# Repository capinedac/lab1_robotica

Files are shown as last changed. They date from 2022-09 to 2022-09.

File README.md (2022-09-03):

# Laboratorio 1 - Robótica Industrial No.1 
Equipo de trabajo: 
- Luis Alberto Chavez Castro
- Camilo Pineda Correa
 
## Desarrollo de la herramienta
Para el proceso de fabricación de la herramienta, este se desarrolló primero físicamente, teniendo en cuenta las medidas de ajuste con el portaherramienta para su implementación, y a partir de este se generó el modelo CAD con ayuda del software Catia.
 
La herramienta tuvo una primera versión que fue probada, se puede visualizar en su montaje al robot articulado:
 
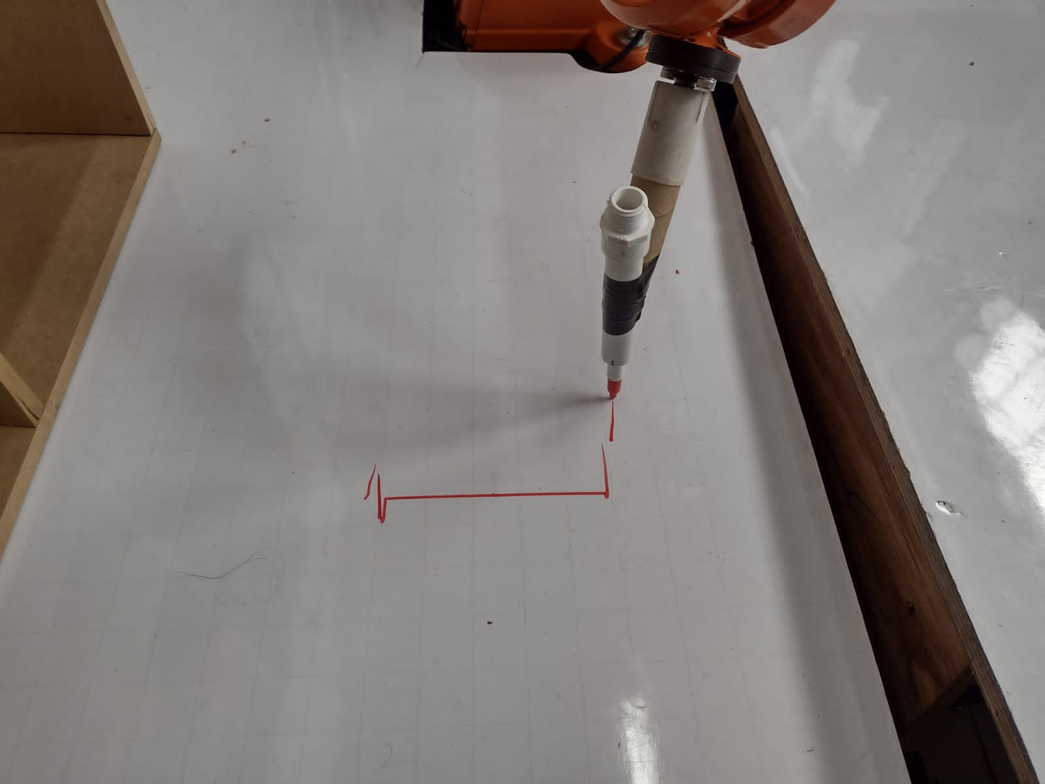
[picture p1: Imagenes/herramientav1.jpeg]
Herramienta v1

 
Su versión final diseñada es la siguiente:
 
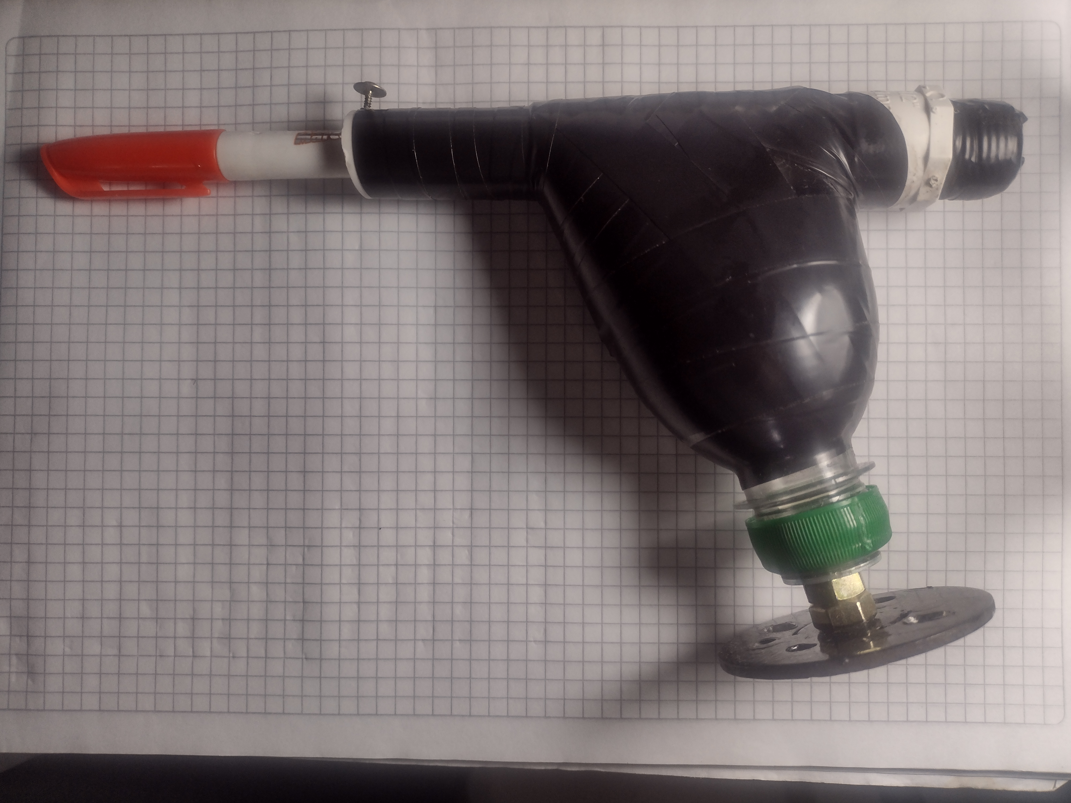
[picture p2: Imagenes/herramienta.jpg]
Foto herramienta

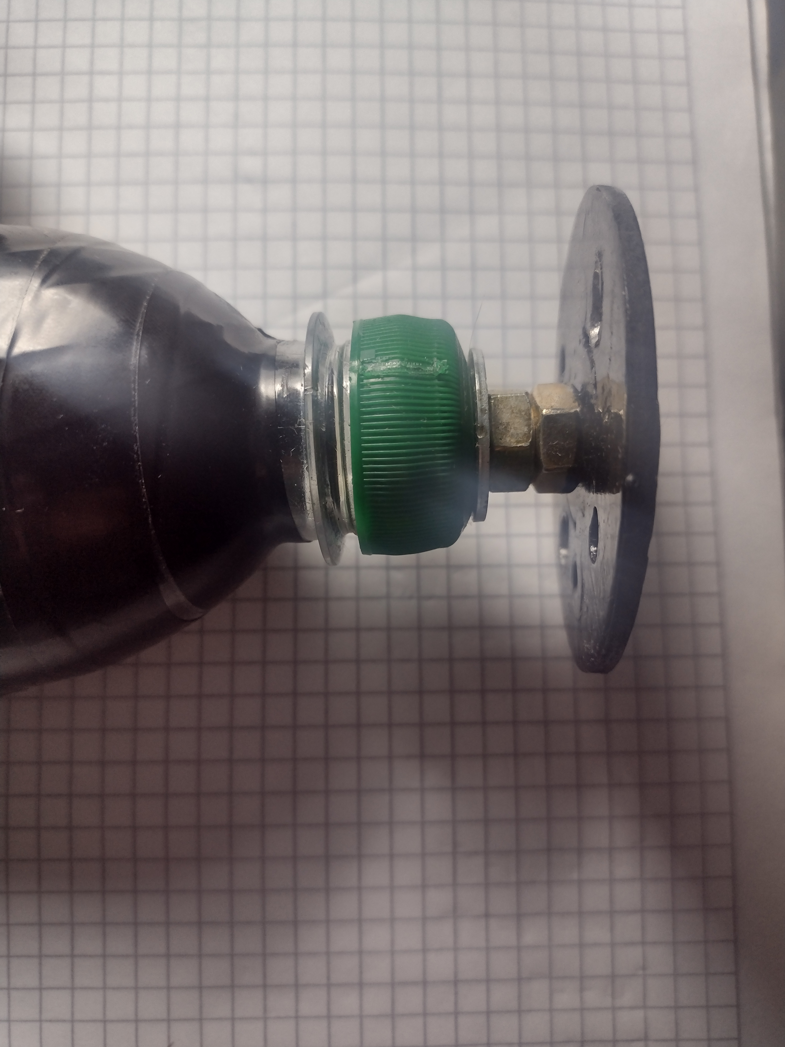
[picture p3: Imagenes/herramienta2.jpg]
Foto 2 herramienta

 
Y su modelo CAD obtenido fue:
 
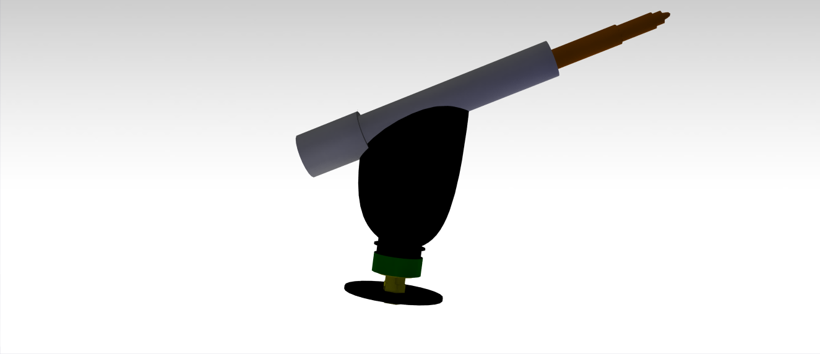
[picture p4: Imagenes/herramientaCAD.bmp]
CAD herramienta

 
Se construyó una herramienta inicial la cual se buscó desde un comienzo que su eje primitivo de diseño no se encontrara sobre el eje Z del TCP del plato portaherramientas a fin de evitar las singularidades del robot, para esto las dos primitivas de diseño empleadas fueron dos líneas coplanares que no fueran paralelas con un ángulo entre ellas de 120º.
Además al realizar las primeras pruebas con el manipulador, se encontró que la herramienta vibraba mucho y era inestable a la hora de ser colocada sobre la superficie plana para trazar, por lo que se planteó un incremento en los  momentos de inercia que evitase el movimiento de la pieza, sin embargo como uno de los requerimientos de diseño que presentados considera el bajo peso para la reducción de cargas inerciales del robot, se planteó emplear materiales pero todos en diferentes medidas incrementaron los momentos de inercia, así que se planteó realizar una ampliación de la geometría de la zona que presentaba la mayor oscilación con materiales ligeros, de fácil consecución y simétricos, para lo cual el candidato seleccionado resultó ser un envase PET (polietilen-Tereftalato) de agua de 500ml, el cual por su peso ligero y alta resistencia mecánica al desgaste por vibraciones, entregó un gran comportamiento al mantener el bajo peso y reducir considerablemente la vibración de la herramienta.

Además de la reducción de cargas inercial , el candidato PET también aportó dos funcionalidades inesperadas, la primera al tener tapa enroscable se puede crear una pieza de ensamble y desensamble cómodo sobre el manipulador que además permite la orientación de la herramienta, sin interferir con la fijación del portaherramientas ni del plato porta herramienta del manipulador IRB140. La segunda cualidad hallada es la posibilidad de aportar carga inercial al emplear el envase como un receptáculo capaz de albergar un volumen de 7 onzas aproximadamente, suficiente para emplear la herramienta de geometría definida en entornos con diversas cargas inerciales que puedan ayudar a realizar experimentos de caracterización inercial de componentes. 
 
plano herramienta
 
En el diseño se cuenta con un sistema de suspensión telescópico entre el marcador y la estructura de forma que hay 40mm entre la punta del marcador y la posición de máxima retracción del elemento a fin de buscar evitar cargas sobre el manipulador robótico; está diseñado de forma predictiva ante una posible colisión, que inicialmente causaría la retracción del elemento antes de activar una pieza fusible causando la fractura de la tapa del envase con lo que la pieza se desprende del manipulador evitando posibles daños al mismo.
 
El sistema de suspensión telescópico se compone de un par de tubos coaxiales
con un ajuste deslizante, lubricado por aceite SAE50, al interior del tubo de mayor diámetro (22mm exterior) también se aloja un resorte, con k=0.1N/m.

## Desarrollo del plano de trabajo y letras
Para el plano de trabajo, este es un tablero inclinado de dimensiones 300mm x 300mm y una inclinación de 45°, diseñado con el software Inventor. Sobre el plano que se trabaja se escribió el texto con las letras a escribir, permitiendo realizar un grabado a través de extrusión de corte de esa figura, lo que permitía contar con el perfil a seguir a través del contorno generado:
 
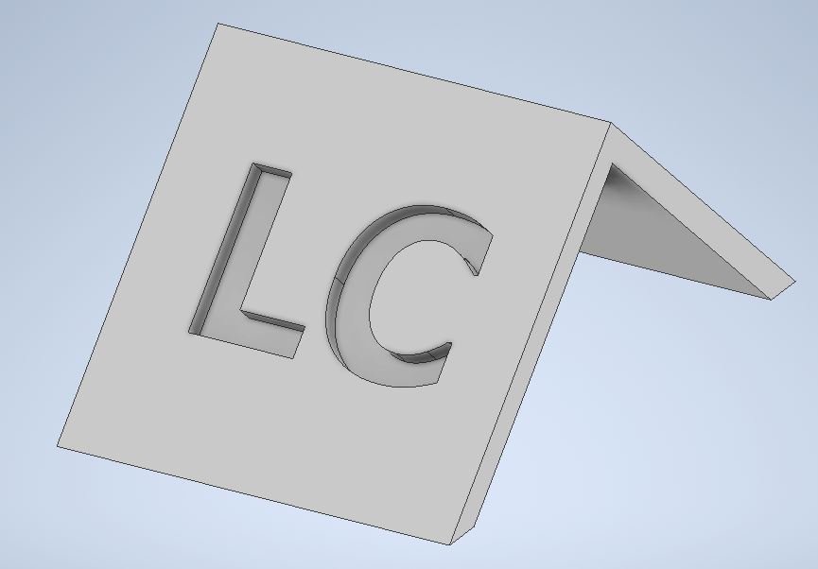
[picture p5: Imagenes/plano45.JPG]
CAD plano45


## Trabajo en RobotStudio.  
Inicialmente se genera la estación de trabajo con el robot articulado IRB 140 y su respectivo controlador RobotWare 6.13.04. Luego se procede a importar la geometría de la herramienta y ajustarla al portaherramientas:
 
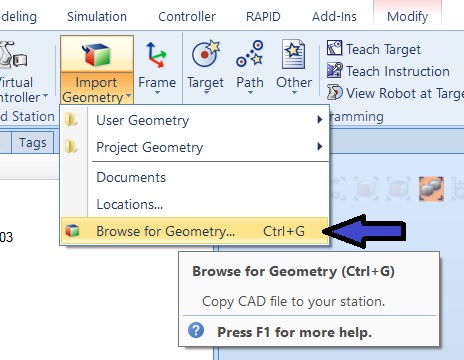
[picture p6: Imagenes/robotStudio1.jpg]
Importar herramienta RobotStudio
  
 
Fue necesario hacer una modificación en cuanto a orientación y desplazamiento para un mejor ajuste, por lo que se accede a la siguiente configuración:
 
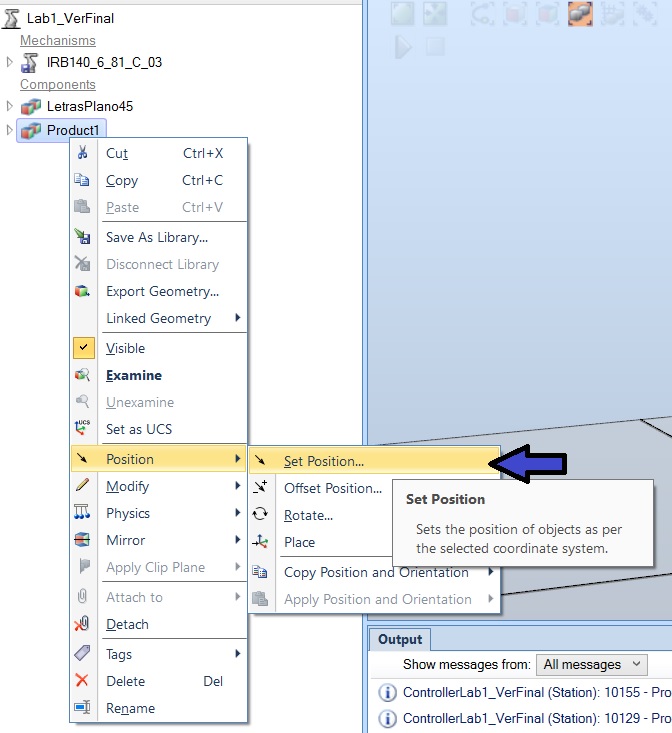
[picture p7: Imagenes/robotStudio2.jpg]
Ajustar herramienta RobotStudio
  
 
Luego, se continúa generando el TCP de la herramienta, para ello se crea el dato de la herramienta teniendo en cuenta la geometría de la herramienta, definiendo un desfase en X de 139.17mm, un desfase en Z de 184.72mm y una rotación sobre el eje Y de 61.7°, valores obtenido gracias a la función snap object y seleccionar la punta de la herramienta:
 
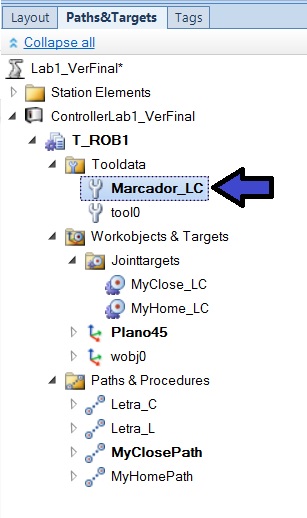
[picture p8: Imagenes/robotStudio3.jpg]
Creación Data Tool

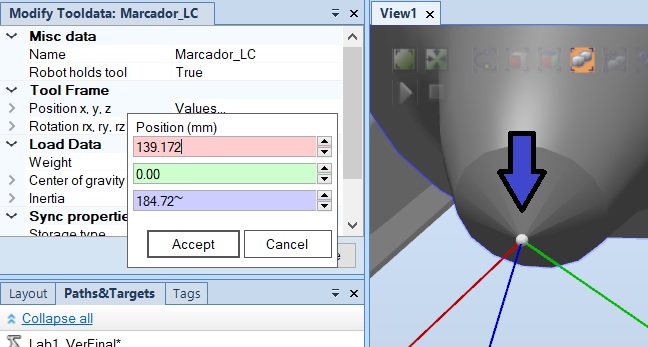
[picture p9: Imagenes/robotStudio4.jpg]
Creación Data Tool 2
  
 
Luego se importa la geometría que contiene los perfiles de las letras y se modifica orientación y posicionamiento para ubicarlo de una forma óptima y que cumpla con ubicarse en el cuadrante X+ Y+.
 
Se generan las trayectorias al seleccionar los contornos de los perfiles y se les ajusta velocidad y zona.
 
Además se generaron 2 jointtarget para definir el home y un punto cercano al plano pero alejado, lo que permitió hacer sus respectivas rutinas agregándolas a un path de forma individual.
 
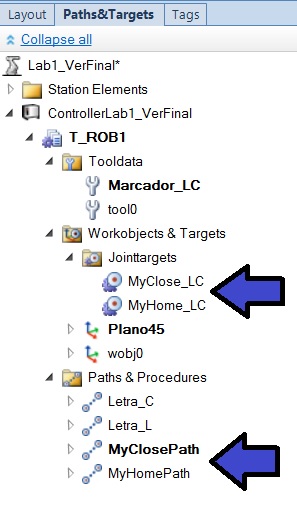
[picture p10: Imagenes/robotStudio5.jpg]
Creación Jointtarget


## Resultados
### Videos
Tras el desarrollo del laboratorio se presentaron inconvenientes para ser completado en su totalidad, se cuenta con la simulación en RobotStudio (“SimulacionRobotStudio”) y una ejecución al aire del código (“VideoEjecucionAlAire”), vídeos alojados dentro del repositorio en la carpeta “Videos”. 
 
Su montaje en el robot articulado IRB 140 se puede visualizar en la siguiente figura:
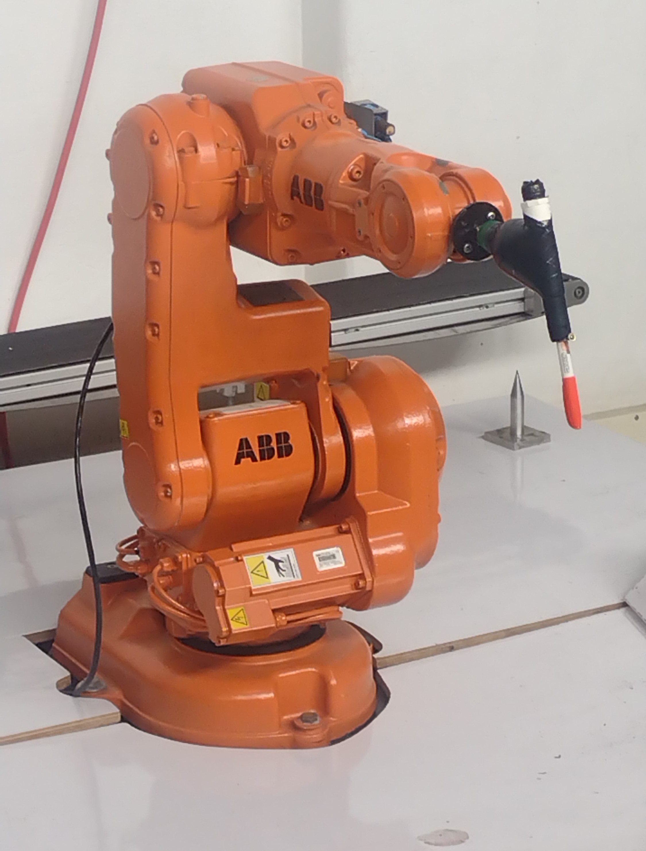
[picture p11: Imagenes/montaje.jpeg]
montaje
  

### Código RAPID
#### Código para trayectoria en plano inclinado a 45°.  
```rapid
MODULE Module1
        CONST robtarget Target_10:=[[-61.252986291,204.835773881,99.999999785],[0,0.999944963,-0.010491487,0],[0,1,-2,0],[9E+09,9E+09,9E+09,9E+09,9E+09,9E+09]];
    CONST robtarget Target_20:=[[-61.252986291,204.835773777,-0.000000215],[0,0.999944963,-0.010491487,0],[0,2,-2,0],[9E+09,9E+09,9E+09,9E+09,9E+09,9E+09]];
    CONST robtarget Target_30:=[[-61.252986291,84.835773776,-0.000000089],[0,0.999944963,-0.010491487,0],[0,2,-2,0],[9E+09,9E+09,9E+09,9E+09,9E+09,9E+09]];
    CONST robtarget Target_40:=[[-91.39885339,84.835773776,-0.000000089],[0,0.999944963,-0.010491487,0],[0,2,-2,0],[9E+09,9E+09,9E+09,9E+09,9E+09,9E+09]];
    CONST robtarget Target_50:=[[-91.39885339,181.98326162,-0.000000191],[0,0.999944963,-0.010491487,0],[0,2,-2,0],[9E+09,9E+09,9E+09,9E+09,9E+09,9E+09]];
    CONST robtarget Target_60:=[[-141.285401202,181.98326162,-0.000000191],[0,0.999944963,-0.010491487,0],[0,1,-2,0],[9E+09,9E+09,9E+09,9E+09,9E+09,9E+09]];
    CONST robtarget Target_70:=[[-141.285401202,204.835773777,-0.000000215],[0,0.999944963,-0.010491487,0],[0,1,-2,0],[9E+09,9E+09,9E+09,9E+09,9E+09,9E+09]];
    CONST robtarget Target_80:=[[-61.252986291,204.835773777,-0.000000215],[0,0.999944963,-0.010491487,0],[0,2,-2,0],[9E+09,9E+09,9E+09,9E+09,9E+09,9E+09]];
    CONST robtarget Target_90:=[[-61.252986291,204.835773881,99.999999785],[0,0.999944963,-0.010491487,0],[0,1,-2,0],[9E+09,9E+09,9E+09,9E+09,9E+09,9E+09]];
    CONST robtarget Target_100:=[[-207.411819355,207.169647462,99.999999783],[0,0.999944963,-0.010491487,0],[0,1,-2,0],[9E+09,9E+09,9E+09,9E+09,9E+09,9E+09]];
    CONST robtarget Target_110:=[[-207.411819355,207.169647358,-0.000000217],[0,0.999944963,-0.010491487,0],[0,1,-2,0],[9E+09,9E+09,9E+09,9E+09,9E+09,9E+09]];
    CONST robtarget Target_120:=[[-164.526892288,190.832532285,-0.0000002],[0,0.999944963,-0.010491487,0],[0,1,-2,0],[9E+09,9E+09,9E+09,9E+09,9E+09,9E+09]];
    CONST robtarget Target_130:=[[-152.638723731,171.189096304,-0.00000018],[0.000000001,0.999944963,-0.010491487,0.000000001],[0,1,-2,0],[9E+09,9E+09,9E+09,9E+09,9E+09,9E+09]];
    CONST robtarget Target_140:=[[-148.676000878,144.933018508,-0.000000152],[0,0.999944963,-0.010491487,0],[0,2,-2,0],[9E+09,9E+09,9E+09,9E+09,9E+09,9E+09]];
    CONST robtarget Target_150:=[[-164.575514654,99.471106029,-0.000000104],[-0.000000001,0.999944963,-0.010491487,0],[0,2,-2,0],[9E+09,9E+09,9E+09,9E+09,9E+09,9E+09]];
    CONST robtarget Target_160:=[[-183.258658901,86.744201652,-0.000000091],[-0.000000001,0.999944963,-0.010491487,0],[0,2,-2,0],[9E+09,9E+09,9E+09,9E+09,9E+09,9E+09]];
    CONST robtarget Target_170:=[[-207.509064087,82.501900194,-0.000000087],[0,0.999944963,-0.010491487,0],[0,2,-2,0],[9E+09,9E+09,9E+09,9E+09,9E+09,9E+09]];
    CONST robtarget Target_180:=[[-231.334023568,85.516486904,-0.00000009],[-0.000000001,0.999944963,-0.010491487,0],[0,2,-2,0],[9E+09,9E+09,9E+09,9E+09,9E+09,9E+09]];
    CONST robtarget Target_190:=[[-248.060117572,92.51810765,-0.000000097],[-0.000000001,0.999944963,-0.010491487,0],[0,2,-2,0],[9E+09,9E+09,9E+09,9E+09,9E+09,9E+09]];
    CONST robtarget Target_200:=[[-248.060117572,121.108059027,-0.000000127],[0,0.999944963,-0.010491487,0],[0,1,-2,0],[9E+09,9E+09,9E+09,9E+09,9E+09,9E+09]];
    CONST robtarget Target_210:=[[-245.045530862,121.108059027,-0.000000127],[0,0.999944963,-0.010491487,0],[0,1,-2,0],[9E+09,9E+09,9E+09,9E+09,9E+09,9E+09]];
    CONST robtarget Target_220:=[[-232.014736696,111.189096305,-0.000000117],[0,0.999944963,-0.010491487,0.000000001],[0,2,-2,0],[9E+09,9E+09,9E+09,9E+09,9E+09,9E+09]];
    CONST robtarget Target_230:=[[-222.825109468,106.764460972,-0.000000112],[0,0.999944963,-0.010491487,0],[0,2,-2,0],[9E+09,9E+09,9E+09,9E+09,9E+09,9E+09]];
    CONST robtarget Target_240:=[[-212.274055983,104.965433419,-0.00000011],[0,0.999944963,-0.010491487,0],[0,2,-2,0],[9E+09,9E+09,9E+09,9E+09,9E+09,9E+09]];
    CONST robtarget Target_250:=[[-200.361576243,107.007572804,-0.000000112],[0.000000001,0.999944963,-0.010491487,0],[0,2,-2,0],[9E+09,9E+09,9E+09,9E+09,9E+09,9E+09]];
    CONST robtarget Target_260:=[[-190.005012223,114.203683014,-0.00000012],[0.000000001,0.999944963,-0.010491487,0],[0,2,-2,0],[9E+09,9E+09,9E+09,9E+09,9E+09,9E+09]];
    CONST robtarget Target_270:=[[-182.663034914,126.602386417,-0.000000133],[0.000000001,0.999944963,-0.010491487,-0.000000001],[0,2,-2,0],[9E+09,9E+09,9E+09,9E+09,9E+09,9E+09]];
    CONST robtarget Target_280:=[[-179.794315303,145.030263241,-0.000000152],[0,0.999944963,-0.010491487,0],[0,1,-2,0],[9E+09,9E+09,9E+09,9E+09,9E+09,9E+09]];
    CONST robtarget Target_290:=[[-182.760279646,163.847118995,-0.000000172],[-0.000000001,0.999944963,-0.010491487,-0.000000001],[0,1,-2,0],[9E+09,9E+09,9E+09,9E+09,9E+09,9E+09]];
    CONST robtarget Target_300:=[[-190.588480619,176.148577666,-0.000000185],[0,0.999944963,-0.010491487,0],[0,1,-2,0],[9E+09,9E+09,9E+09,9E+09,9E+09,9E+09]];
    CONST robtarget Target_310:=[[-200.993667004,182.712597115,-0.000000192],[-0.000000001,0.999944963,-0.010491487,0.000000001],[0,1,-2,0],[9E+09,9E+09,9E+09,9E+09,9E+09,9E+09]];
    CONST robtarget Target_320:=[[-212.468545449,184.706114133,-0.000000194],[0,0.999944963,-0.010491487,0],[0,1,-2,0],[9E+09,9E+09,9E+09,9E+09,9E+09,9E+09]];
    CONST robtarget Target_330:=[[-223.797556794,182.712597115,-0.000000192],[0,0.999944963,-0.010491487,0],[0,1,-2,0],[9E+09,9E+09,9E+09,9E+09,9E+09,9E+09]];
    CONST robtarget Target_340:=[[-240.037427134,173.279858055,-0.000000182],[0,0.999944963,-0.010491487,0],[0,1,-2,0],[9E+09,9E+09,9E+09,9E+09,9E+09,9E+09]];
    CONST robtarget Target_350:=[[-245.33726506,168.660733257,-0.000000177],[-0.000000001,0.999944963,-0.010491487,0],[0,1,-2,0],[9E+09,9E+09,9E+09,9E+09,9E+09,9E+09]];
    CONST robtarget Target_360:=[[-248.060117572,196.861705705,-0.000000206],[0,0.999944963,-0.010491487,0],[0,1,-2,0],[9E+09,9E+09,9E+09,9E+09,9E+09,9E+09]];
    CONST robtarget Target_370:=[[-220.880214816,206.294444764,-0.000000216],[0,0.999944963,-0.010491487,0],[0,1,-2,0],[9E+09,9E+09,9E+09,9E+09,9E+09,9E+09]];
    CONST robtarget Target_380:=[[-207.411819355,207.169647358,-0.000000217],[0,0.999944963,-0.010491487,0],[0,1,-2,0],[9E+09,9E+09,9E+09,9E+09,9E+09,9E+09]];
    CONST robtarget Target_390:=[[-207.411819355,207.169647462,99.999999783],[0,0.999944963,-0.010491487,0],[0,1,-2,0],[9E+09,9E+09,9E+09,9E+09,9E+09,9E+09]];
    CONST jointtarget MyHome_LC:=[[0,0,0,0,30,0],[9E+09,9E+09,9E+09,9E+09,9E+09,9E+09]];
    CONST jointtarget MyClose_LC:=[[0,25,20,170,15,-125],[9E+09,9E+09,9E+09,9E+09,9E+09,9E+09]];
!***********************************************************
    !
    ! Module:  Module1
    !
    ! Description:
    !   <Insert description here>
    !
    ! Author: user
    !
    ! Version: 1.0
    !
    !***********************************************************

    !***********************************************************
    !
    ! Procedure main
    !
    !   This is the entry point of your program
    !
    !***********************************************************
    PROC main()
        !Add your code here
        MyHomePath;
        MyClosePath;
        Letra_L;
        Letra_C;
        MyClosePath;
        MyHomePath;
    ENDPROC
    PROC Letra_L()
        MoveL Target_10,v200,z5,Marcador_LC\WObj:=Plano45;
        MoveL Target_20,v200,z5,Marcador_LC\WObj:=Plano45;
        MoveL Target_30,v200,z5,Marcador_LC\WObj:=Plano45;
        MoveL Target_40,v200,z5,Marcador_LC\WObj:=Plano45;
        MoveL Target_50,v200,z5,Marcador_LC\WObj:=Plano45;
        MoveL Target_60,v200,z5,Marcador_LC\WObj:=Plano45;
        MoveL Target_70,v200,z5,Marcador_LC\WObj:=Plano45;
        MoveL Target_80,v200,z5,Marcador_LC\WObj:=Plano45;
        MoveL Target_90,v200,z5,Marcador_LC\WObj:=Plano45;
    ENDPROC
    PROC Letra_C()
        MoveL Target_100,v200,z5,Marcador_LC\WObj:=Plano45;
        MoveL Target_110,v200,z5,Marcador_LC\WObj:=Plano45;
        MoveL Target_120,v200,z5,Marcador_LC\WObj:=Plano45;
        MoveL Target_130,v200,z5,Marcador_LC\WObj:=Plano45;
        MoveL Target_140,v200,z5,Marcador_LC\WObj:=Plano45;
        MoveL Target_150,v200,z5,Marcador_LC\WObj:=Plano45;
        MoveL Target_160,v200,z5,Marcador_LC\WObj:=Plano45;
        MoveL Target_170,v200,z5,Marcador_LC\WObj:=Plano45;
        MoveL Target_180,v200,z5,Marcador_LC\WObj:=Plano45;
        MoveL Target_190,v200,z5,Marcador_LC\WObj:=Plano45;
        MoveL Target_200,v200,z5,Marcador_LC\WObj:=Plano45;
        MoveL Target_210,v200,z5,Marcador_LC\WObj:=Plano45;
        MoveL Target_220,v200,z5,Marcador_LC\WObj:=Plano45;
        MoveL Target_230,v200,z5,Marcador_LC\WObj:=Plano45;
        MoveL Target_240,v200,z5,Marcador_LC\WObj:=Plano45;
        MoveL Target_250,v200,z5,Marcador_LC\WObj:=Plano45;
        MoveL Target_260,v200,z5,Marcador_LC\WObj:=Plano45;
        MoveL Target_270,v200,z5,Marcador_LC\WObj:=Plano45;
        MoveL Target_280,v200,z5,Marcador_LC\WObj:=Plano45;
        MoveL Target_290,v200,z5,Marcador_LC\WObj:=Plano45;
        MoveL Target_300,v200,z5,Marcador_LC\WObj:=Plano45;
        MoveL Target_310,v200,z5,Marcador_LC\WObj:=Plano45;
        MoveL Target_320,v200,z5,Marcador_LC\WObj:=Plano45;
        MoveL Target_330,v200,z5,Marcador_LC\WObj:=Plano45;
        MoveL Target_340,v200,z5,Marcador_LC\WObj:=Plano45;
        MoveL Target_350,v200,z5,Marcador_LC\WObj:=Plano45;
        MoveL Target_360,v200,z5,Marcador_LC\WObj:=Plano45;
        MoveL Target_370,v200,z5,Marcador_LC\WObj:=Plano45;
        MoveL Target_380,v200,z5,Marcador_LC\WObj:=Plano45;
        MoveL Target_390,v200,z5,Marcador_LC\WObj:=Plano45;
    ENDPROC
    PROC MyHomePath()
        MoveAbsJ MyHome_LC,v200,z5,Marcador_LC\WObj:=Plano45;
    ENDPROC
    PROC MyClosePath()
        MoveAbsJ MyClose_LC,v200,z5,Marcador_LC\WObj:=Plano45;
    ENDPROC
ENDMODULE
```

## Conclusiones
* La definición del Workobject permite trabajar sobre una superficie que pueda tener una disposición diferente a la determinada a través de RobotStudio. Gracias a este, se calibra la ubicación de los 3 puntos que los define y el plano de trabajo se adapta.
* Para el trabajo en RobotStudio es importante tener en cuenta las advertencias al generar las trayectorias, las cuales son reparadas al analizar y seleccionar la pose más conveniente según el movimiento y las posiciones clave que debe alcanzar.  
* La calibración manual de la herramienta con ayuda del brazo IRB 140 puede ser evitado si se cuenta con un completo y correcto modelado de la herramienta, ya que a través del software se define el TCP referente a la punta de la herramienta, sin embargo es recomendado realizar su calibración.    
* Es importante contar con un juego en el diseño de la herramienta, pues en caso de algún choque esta se retracte y evite algún inconveniente como dañar la máquina, le herramiento o golpear algún otro elemento.

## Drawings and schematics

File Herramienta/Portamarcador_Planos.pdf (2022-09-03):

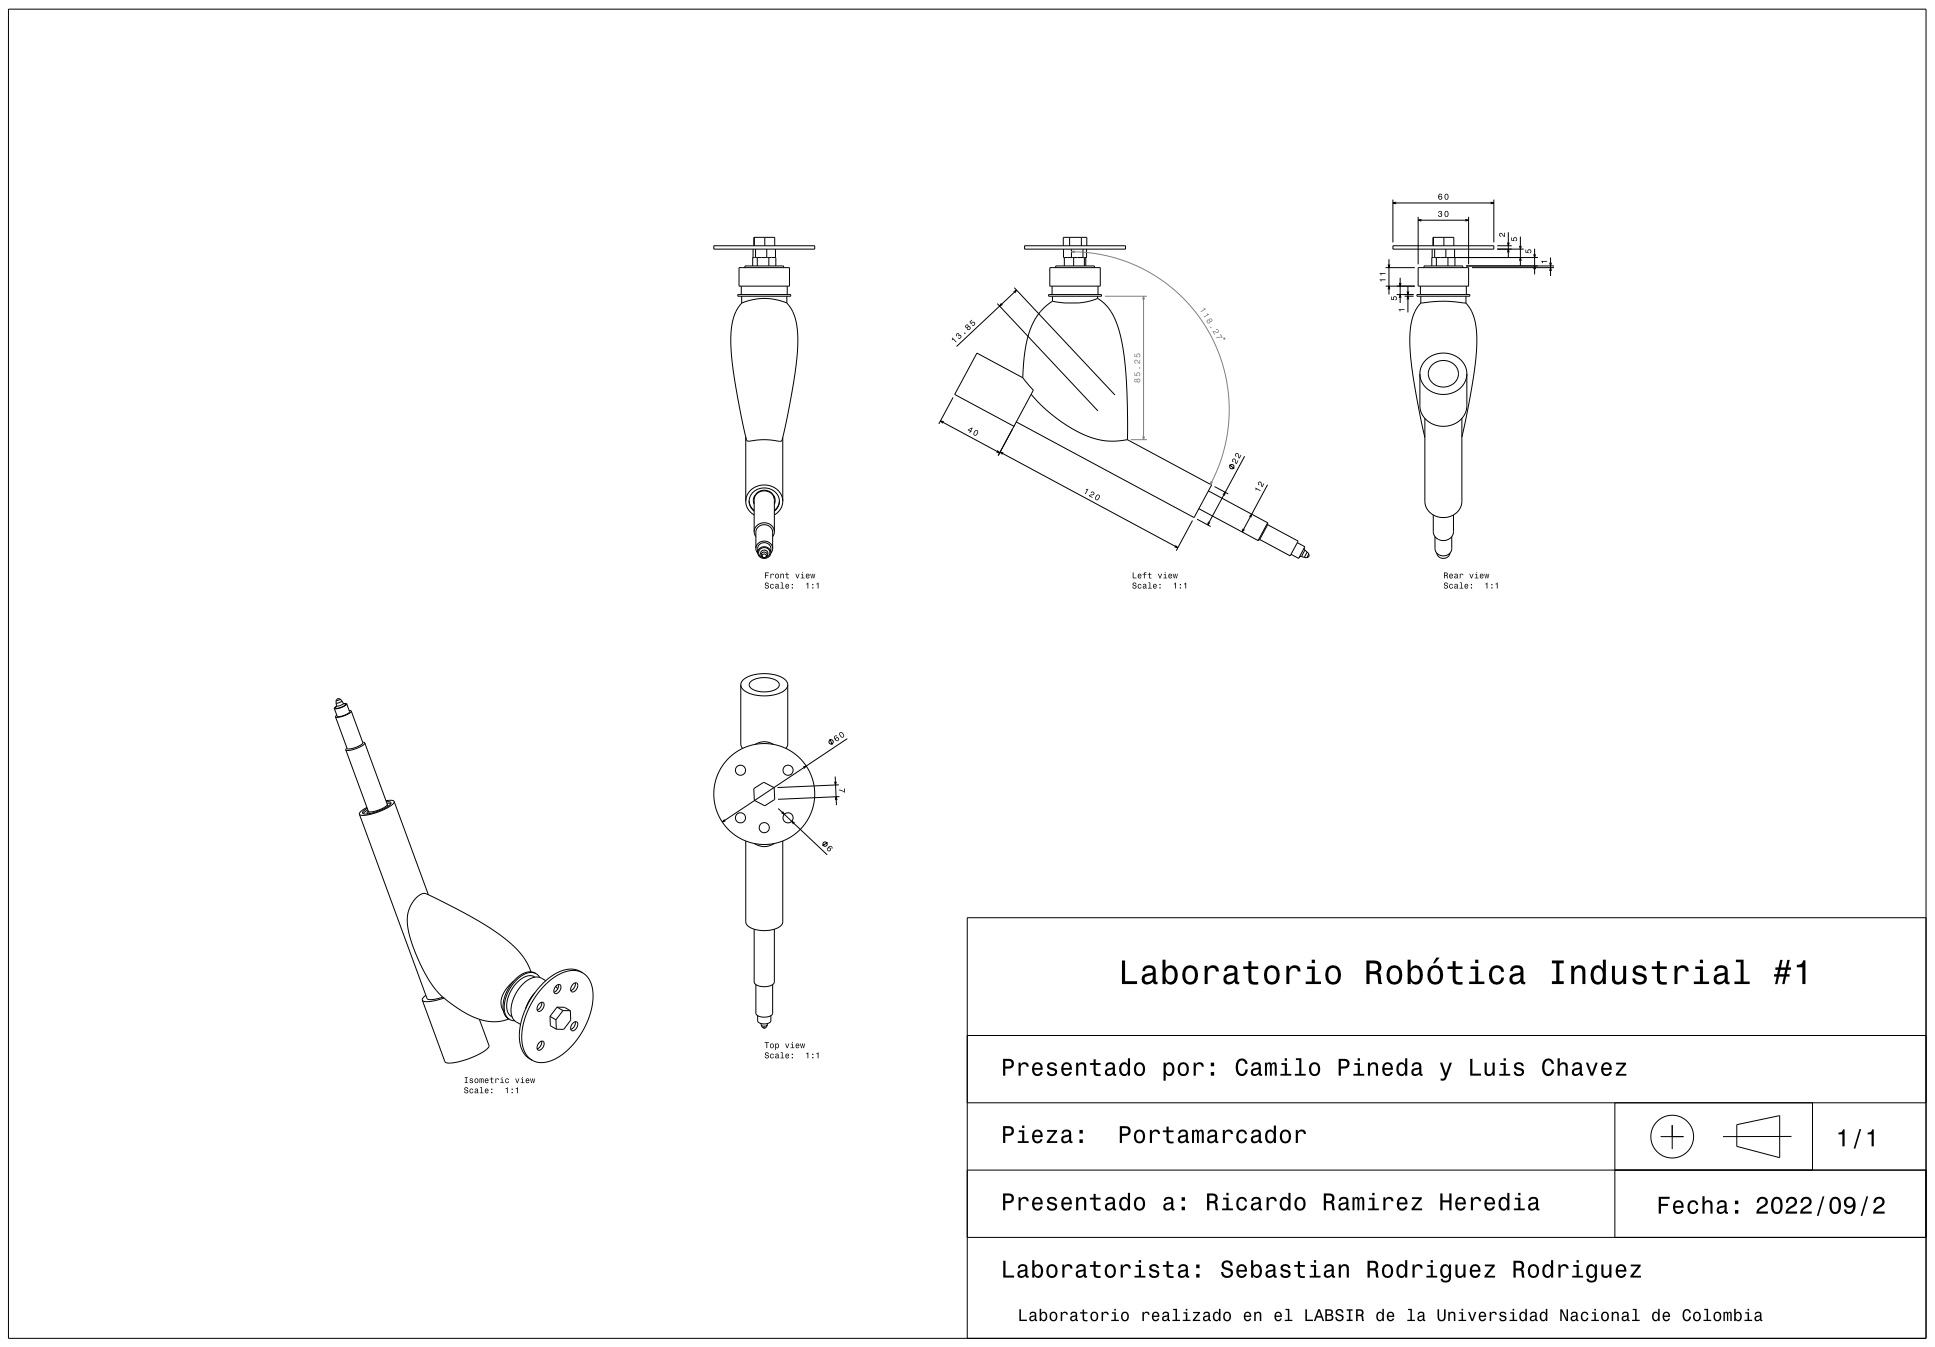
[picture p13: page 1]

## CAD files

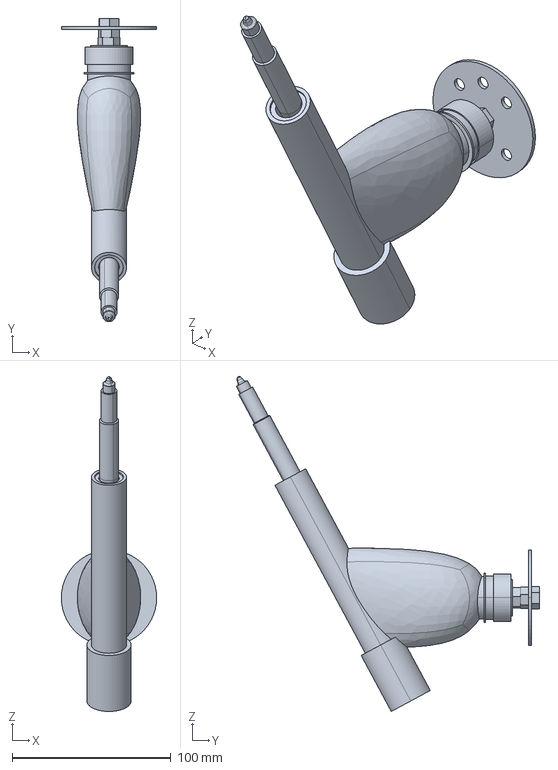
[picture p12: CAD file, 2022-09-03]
Herramienta/Product1.stp
60.0 x 190.8 x 210.7 mm
